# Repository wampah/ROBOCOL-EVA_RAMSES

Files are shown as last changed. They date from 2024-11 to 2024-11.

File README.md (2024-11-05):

# Mecanismo de extracción de muestras y laboratorio de evaluación de presencia de vida para un rover de exploración a distancia

Este repositorio contiene los archivos CAD y el código de Arduino del laboratorio de detección de vida alienígena, E.V.A. (Evaluador de Vida Alienígena), y del sistema de extracción de muestras, RAMSES (Recolector y Analizador de Muestras SuperficialES), desarrollados para el rover de la competencia University Rover Challenge (URC) 2022.

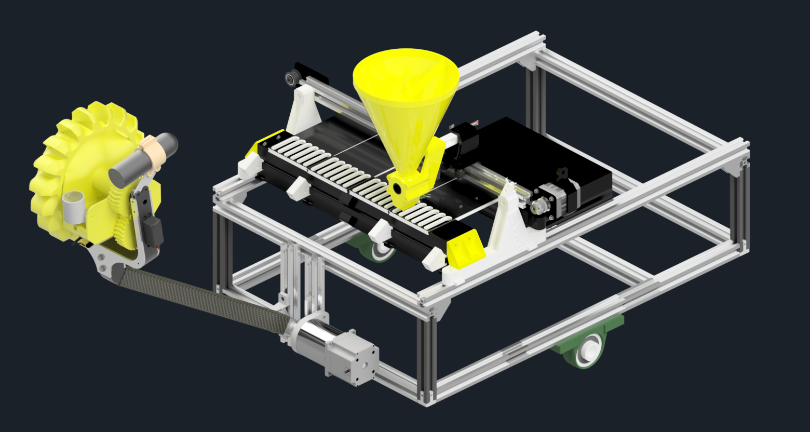
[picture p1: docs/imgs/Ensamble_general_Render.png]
Render EVA y RAMSES


## Descripción del Proyecto

### 1. **E.V.A. - Evaluador de Vida Alienígena**
E.V.A. es un sistema automatizado de análisis que permite la evaluación de vida alienígena en hasta 4 muestras simultáneas mediante 6 pruebas químicas distintas, ofreciendo datos sobre la presencia o ausencia de vida. Las muestras se distribuyen en 24 compartimentos mediante un actuador lineal de correa, y se dosifican utilizando un dispensador rotativo controlado por un servomotor de rotación continua y una válvula flexible en TPU. Una celda de carga mide el peso dosificado, y una cámara observa las reacciones químicas en cada compartimento. 

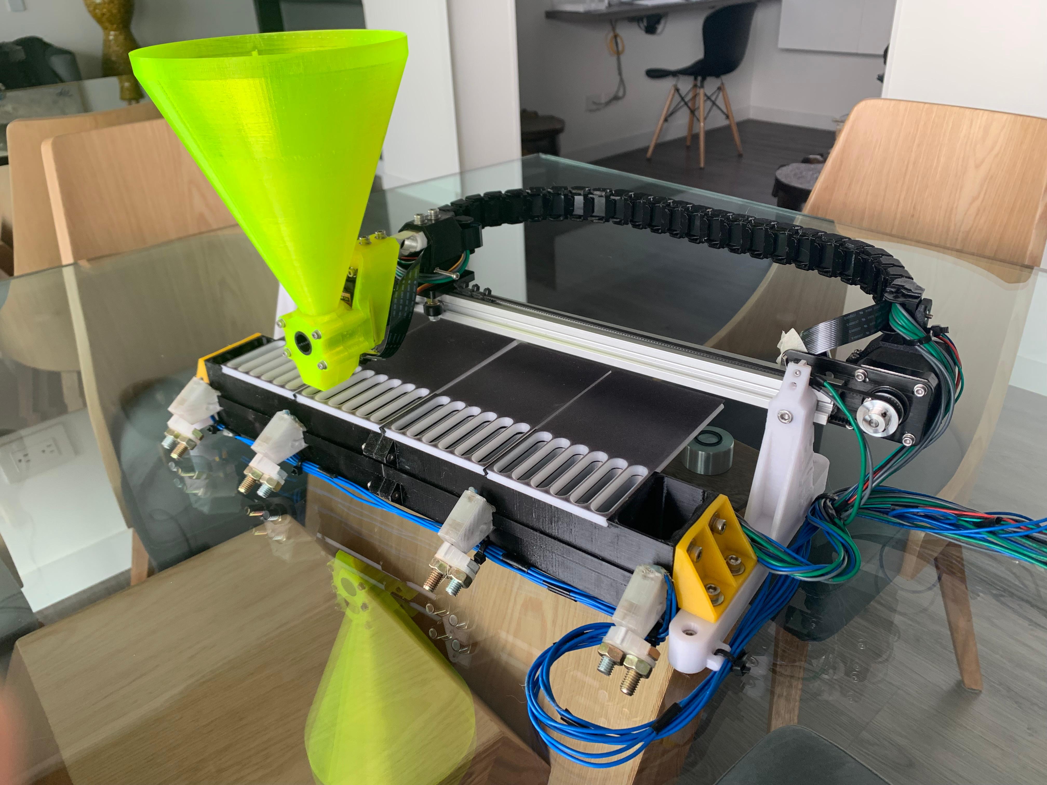
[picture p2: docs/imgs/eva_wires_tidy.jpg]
EVA


EVA gif

- **Pruebas químicas**: Detecta biomoléculas inorgánicas y orgánicas, como sales minerales y proteínas, usando reactivos especializados. 
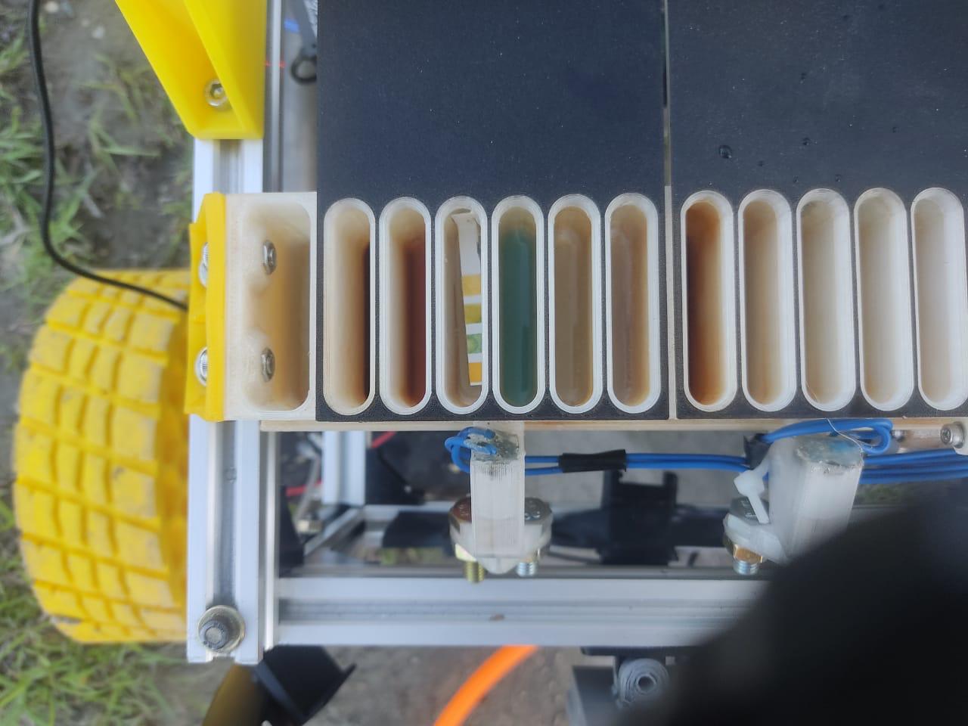
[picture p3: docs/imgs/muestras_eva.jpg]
EVA reactivos
  
- **Componentes principales**: Actuador lineal, servomotor, celda de carga, cámara, motores vibradores.
- **Fabricación**: Varias piezas fueron impresas en 3D, incluyendo compartimentos, tapas, soportes y el dispensador.

### 2. **RAMSES - Sistema de Extracción de Muestras**
RAMSES es el sistema encargado de recolectar, tamizar y medir la temperatura y humedad de las muestras antes de transferirlas a E.V.A. para su análisis. El sistema utiliza componentes impresos en 3D y un brazo controlado por un motor NEMA23 con reducción de 1:15, que permite el posicionamiento preciso del cabezal de excavación.

- **Funciones**: Recolección de muestras, tamizado, medición de temperatura y humedad.
- **Fabricación**: La mayoría de las piezas están fabricadas con impresión 3D.

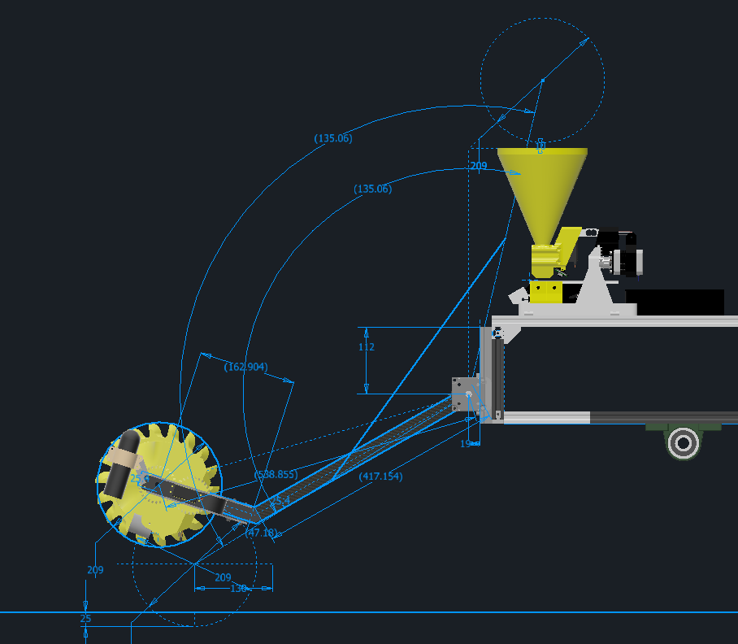
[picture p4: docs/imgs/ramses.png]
RAMSES


RAMSES gif

### 3. **Caja Electrónica**
La caja de electrónica aloja los componentes electrónicos del subsistema de sensórica y extracción, protegiéndolos de condiciones ambientales adversas. 

---

## Contenido del Repositorio

El repositorio se estructura en las siguientes carpetas y archivos:

- **Caja Electronica**: Archivos CAD de la caja de electrónica.
- **code**: Archivos de código de Arduino que controlan los subsistemas.
- **EVA**: Archivos CAD del sistema E.V.A.
- **Extras**: Archivos CAD complementarios.
- **Ready to print files**: Archivos CAD listos para impresión 3D de diversas piezas.
- **Sistema de extracción**: Archivos CAD del sistema RAMSES.
- **Ensamble general.iam**: Ensamble general del rover, integrando E.V.A., RAMSES y otros subsistemas.

## Instrucciones de Uso

1. **Montaje**: Ensamble los sistemas siguiendo los modelos CAD disponibles.
2. **Programación**: Cargue el código en los controladores Arduino. El sistema está configurado para comunicarse con una Raspberry Pi 4, conectada a través de serial para el control de actuadores y lectura de sensores.
3. **Operación**: Los reactivos se deben pre-cargar en los compartimentos de E.V.A. antes de la competencia. El sistema RAMSES extraerá muestras y las transferirá a E.V.A. para su análisis.

## Créditos y Equipo

El diseño, prototipado, y manufactura de estos sistemas fueron realizados por el equipo de Robocol de la Universidad de los Andes, en colaboración con miembros de diversas disciplinas. Estos sistemas formaron parte del rover de Robocol, que compitió en la URC 2022, y están diseñados para proporcionar datos relevantes para la detección de vida en condiciones simuladas de Marte.

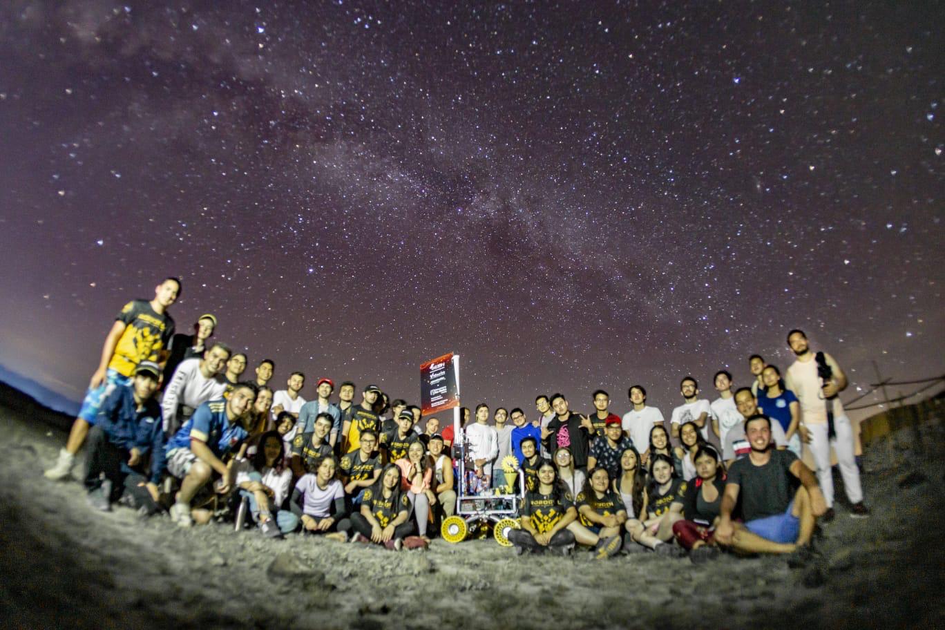
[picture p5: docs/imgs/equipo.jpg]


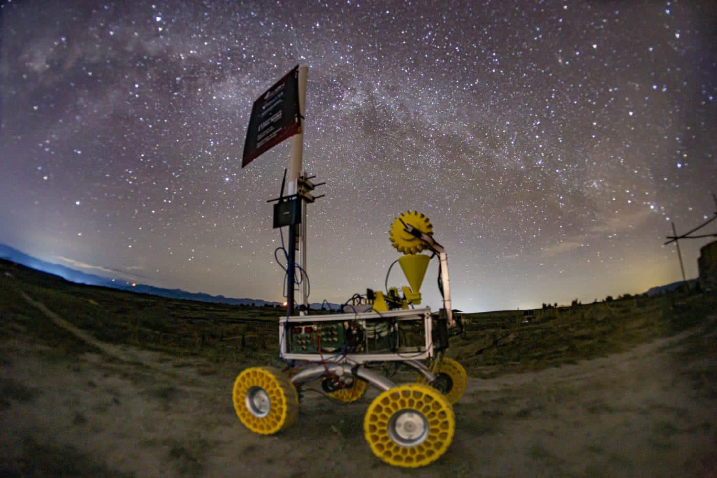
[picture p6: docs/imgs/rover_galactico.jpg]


### Contacto
Para consultas sobre este proyecto, puedes contactar a [Robocol](https://www.instagram.com/robocol/).

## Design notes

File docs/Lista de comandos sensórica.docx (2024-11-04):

Lista de comandos

¡¡¡¡Nota para sensórica -> TODOS LAS FUNCIONES DE MOVIMIENTO O QUE ESPERAN UNA ENTRADA DEBEN TENER TIMEOUT!!!!

ENVIAR UN MENSAJE DE READY O DE FINALIZACIÓN POR SERIAL

Mover el EVA (MOVE)

- M (# de compartimiento)
- Descripción:
  - Mueve el dispensador del EVA a la caja deseada.
- Notas:
  - El número de caja es un número de 2 dígitos. Rango [00,24].
- Ejemplos:
  - “M05“
  - “M24“

Abrir/cerrar cajas (BOX)

- B (# caja) (estado)
- Descripción:
  - Abre o cierra la puerta de la caja deseada.
- Notas:
  - El número de caja es un número de 1 dígito. Rango [1,4]
  - El estado es un dígito. Booleano. Rango [0,1]
- Ejemplos:
  - “B10“
  - “B11“
  - “B21“

Vibrar (SHAKE)

- S (tiempo en segundos)
- Descripción:
  - Agita las cajas del EVA por un tiempo determinado.
- Notas:
  - El tiempo es un número de 2 dígitos. Rango [00,99]
- Ejemplos:
  - “S05”
  - “S10”

Homear (HOME)

- H (sistema)
- Descripción:
  - Hace el home del sistema deseado (EVA o sistema de extracción)
- Notas:
  - El sistema es un carácter que indica el sistema. E para el EVA, X para el sistema de extracción. {“E”,”X”}
- Ejemplos:
  - “HE”
  - “HX”

Limpiar embudo (CLEAN)

- C (Velocidad)
- Descripción:
  - Determina la velocidad del motor de limpieza del embudo. En velocidad 0 se apaga.
- Notas:
  - La velocidad es un número de 1 carácter. Rango [0,5]
- Ejemplos:
  - “C0”
  - “C4”

Dispensar (DISPENSE)

- D (cantidad de muestra en gramos)
- Descripción:
  - Dispensa la cantidad de muestra deseada en gramos
- Notas:
  - La cantidad es un número de 2 dígitos. Rango [00,99]
- Ejemplos:
  - “D01”
  - “D05”

Encender/apagar sistemas (ENABLE)

- E (sistema) (estado)
- Descripción:
  - Habilita o deshabilita la potencia a los motores de paso del sistema deseado (EVA o sistema de extracción)
- Notas:
  - El sistema es un carácter que indica el sistema. E para el EVA, X para el sistema de extracción. {“E”,”X”}
  - El estado es un dígito. Booleano. Rango [0,1]
- Ejemplos:
  - “EE1”
  - “EX0”

Mover brazo (ARM)

- A (posición)
- Descripción:
  - Mueve el brazo a la posición superior o inferior
- Notas:
  - La posición es indicada por un carácter. U para la posición de arriba, D para la posición de extracción. {“U”,”D”}
- Ejemplos:
  - “AU“
  - “AD“

Extraer muestra (EXTRACT)

- X (velocidad) (tiempo)
- Descripción:
  - Gira la rueda de extracción a una velocidad determinada, por un tiempo determinado. El tamiz se prende mientras se extrae y se queda prendido un tiempo después para limpiarse.
- Notas:
  - La velocidad es un número de 1 carácter. Rango [0,5]
  - El tiempo es un número de 2 caracteres. Rango [00,99]
- Ejemplos:
  - “X105“
  - “X510“

Dejar muestra en el EVA (GATHER)

- G
- Descripción:
  - Dispensa la muestra recolectada por el sistema de extracción al EVA.
- Notas:
  - El sistema de extracción debe estar en la posición de arriba.
- Ejemplos:
  - “G“

COMANDOS DE CONTROL MANUAL:

Mover el EVA manualmente (MANUAL MOVE)

- -M (dirección) (distancia en mm)
- Descripción:
  - Mueve el dispensador del EVA manualmente.
- Notas:
  - La dirección es un dígito. Booleano. 0 indica mover en una dirección, 1 la otra dirección. Rango [0,1]
  - La distancia es un número de tres dígitos. Rango [000,999]
- Ejemplos:
  - “-M1100“
  - “-M0050“

Dispensar manualmente (MANUAL DISPENSE)

- -D (velocidad) (tiempo en segundos)
- Descripción:
  - Dispensa muestra manualmente
- Notas:
  - La velocidad es un número de 1 carácter. Rango [0,5]
  - El tiempo es un número de 1 carácter. Rango [0,9]
- Ejemplos:
  - “-D55”
  - “-D14”

Mover brazo manualmente (MANUAL ARM)

- -A (dirección) (distancia en grados)
- Descripción:
  - Mueve el brazo manualmente
- Notas:
  - La dirección es un dígito. Booleano. 0 indica mover en una dirección, 1 la otra dirección. Rango [0,1]
  - La distancia es un número de tres dígitos. Rango [000,999]
- Ejemplos:
  - “-A1100“
  - “-A0050“

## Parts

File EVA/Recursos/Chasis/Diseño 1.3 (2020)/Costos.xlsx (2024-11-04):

Costos Tracción
Componente | Referencia | Material | Costo/Unidad | Cantidad | Total
Rótula | PHS10 | Acero/Aluminio | 15126 | 6 | $90756.00
Chumacera | UCF 204-12 SS | Acero/Plástico | 40336 | 1 | $40336.00
Anillos Seeger | A 19 | Acero | 168 | 10 | $1680.00
IVA |  |  |  |  | $25226.68
 |  |  |  | Total Reprefer | $157998.68
 |  |  |  | En el recibo | $158000.00
Barra roscada | M10x1,5 de 1 m de largo | Acero | 9075.6 | 2 | $18151.20
Tornillos Bristol | M5 de 70 mm de largo | Acero | 420.17 | 20 | $8403.40
IVA |  |  |  |  | $5045.37
 |  |  |  | Total 7777777 | $31599.97
 |  |  |  | En el recibo | $31600.00
Potenciómetro | 20 K ohm de 10 vueltas | Plástico/Cobre/Acero | 13000 | 1 | $10530.00
IVA |  |  |  |  | $2470.00
 |  |  |  | Total Electrónicas Netronic | $13000.00
 |  |  |  | En el recibo | $13000.00
 | GRAN TOTAL | $202600.00

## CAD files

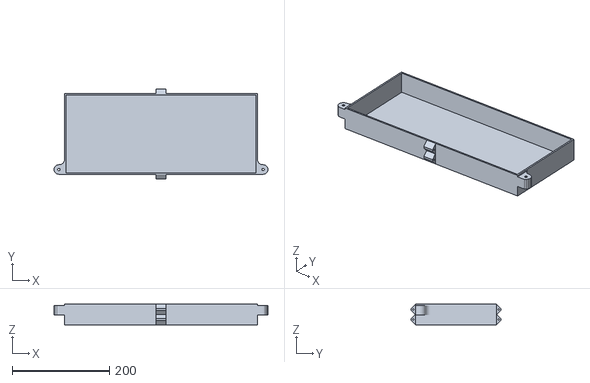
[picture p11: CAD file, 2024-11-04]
Caja Electronica/V2/Caja de electrónica.stl
440.0 x 184.6 x 43.0

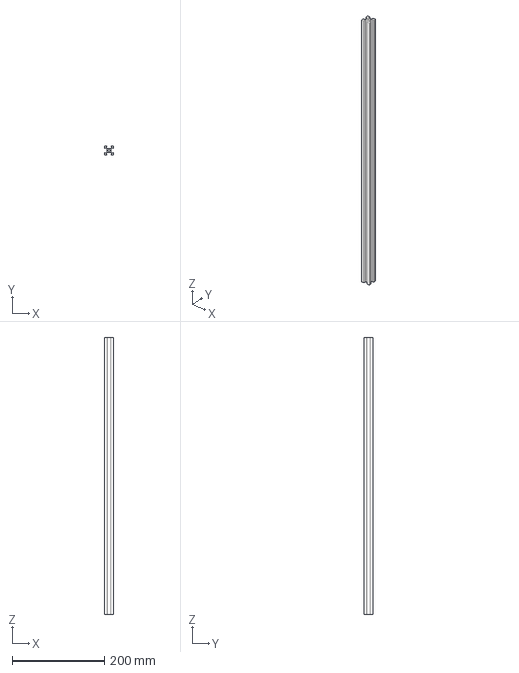
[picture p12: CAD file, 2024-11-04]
EVA/Recursos/Chasis/Diseño 1.3 (2020)/Step files/20x20mm L.stp
20.0 x 20.0 x 600.0 mm

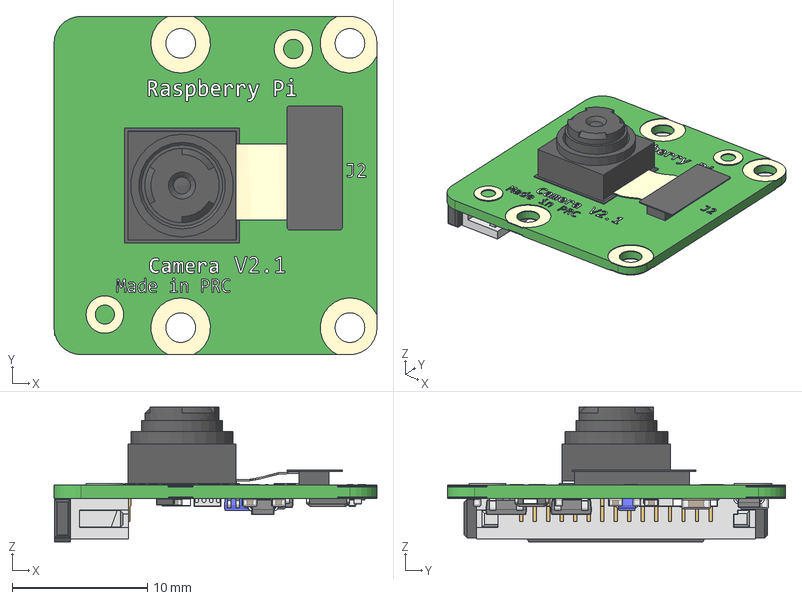
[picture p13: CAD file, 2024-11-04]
EVA/Recursos/Pi Camera/OTHER_FORMATS/RspCameraMia.stp
23.9 x 25.0 x 9.96 mm
PicameraPCB
OVA5647_Housing
OVA5647_Lens_FOV
ribbon_cam
CCD
CAPC-0805-T0.75-BN x 2
CAPC-0402-T0.55-BN x 10
RESC-0402 x 3
RESC-0603 x 2
RESC-1210
c-1-1734248-5-e-raspberry_display
SOT23-5 x 3
KX7 SMD Quartz Crystal Resonator 3.2x2.5mm
c6aaa
4pin_smd x 3

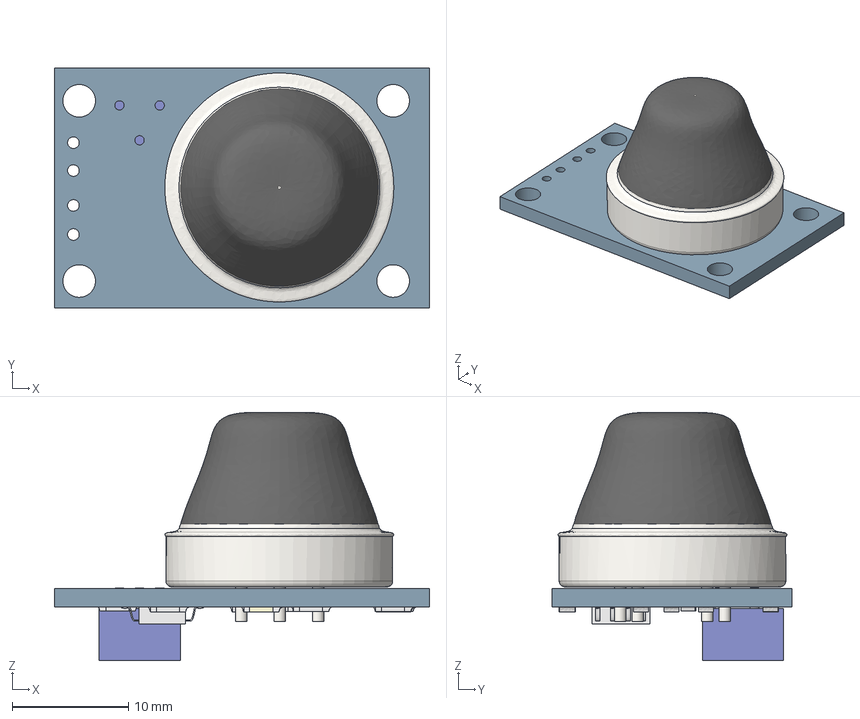
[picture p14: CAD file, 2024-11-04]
EVA/Recursos/Sensores/MQ2/MQ-2.step
32.2 x 20.6 x 21.4 mm
PCB
sensor
10k ohm SMT x 7
leads

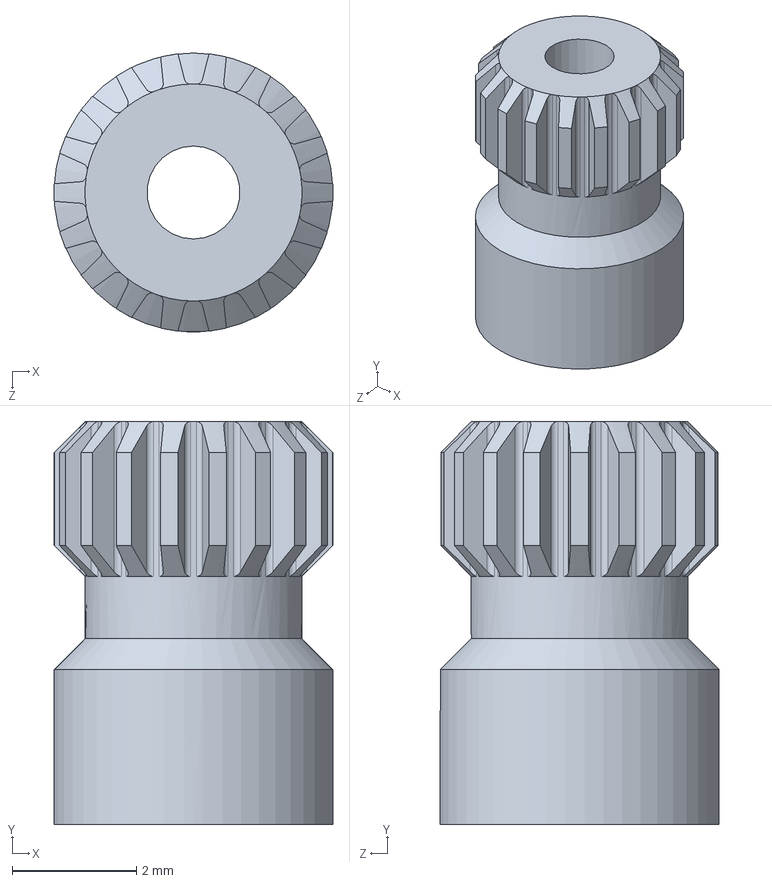
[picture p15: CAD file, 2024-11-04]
EVA/Recursos/Servo MG90S/Part4.SLDPRT
4.50 x 6.50 x 4.50 mm

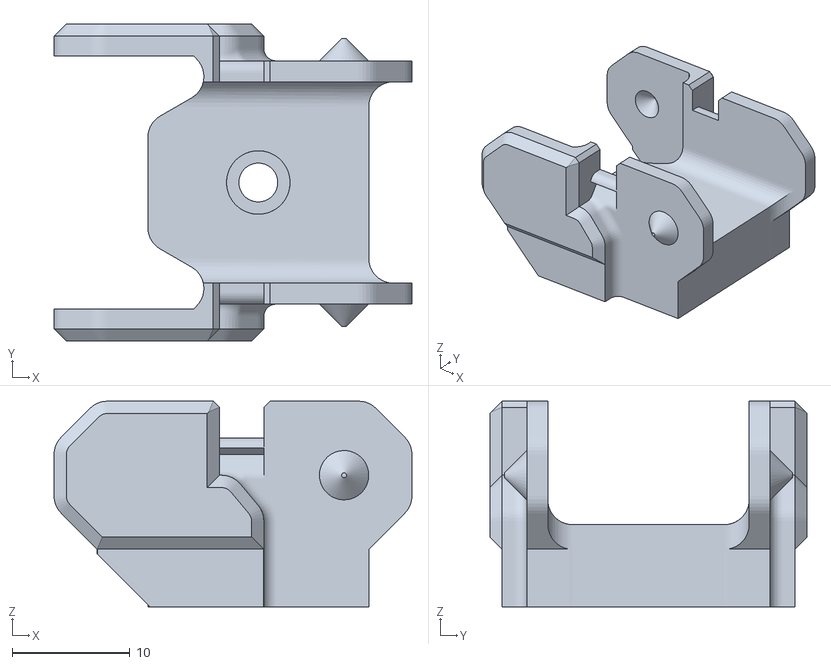
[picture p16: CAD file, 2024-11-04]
EVA/V3 (Actual)/Acople a chasis/Chainlink modificado.stl
30.5 x 27.0 x 17.5

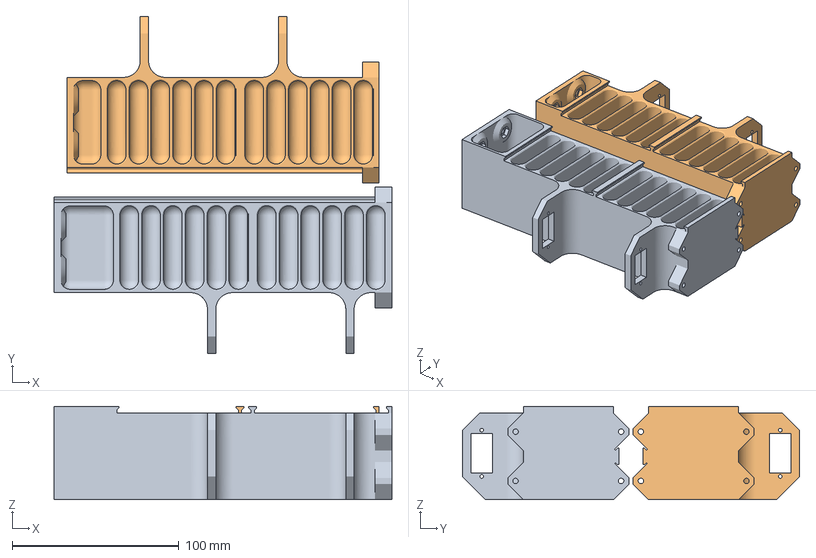
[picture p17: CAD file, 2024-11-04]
EVA/V3 (Actual)/cajas_V2.3mf
202.5 x 202.2 x 56.0 mm
cajas_V2.stl x 2

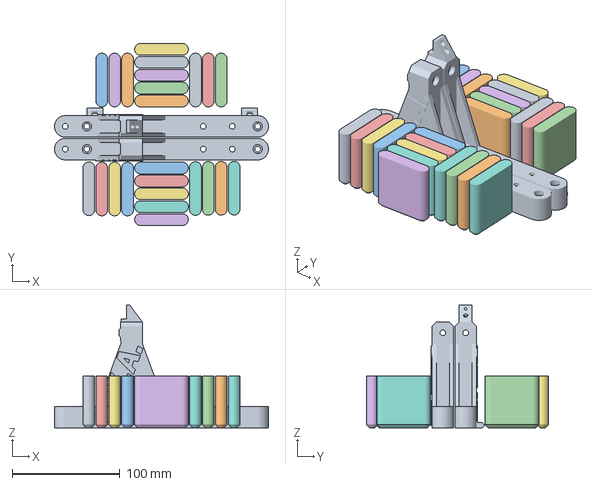
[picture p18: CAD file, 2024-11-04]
Ready to print files/Part2.3mf
198.5 x 168.8 x 114.0 mm
Merged
Part2.stl

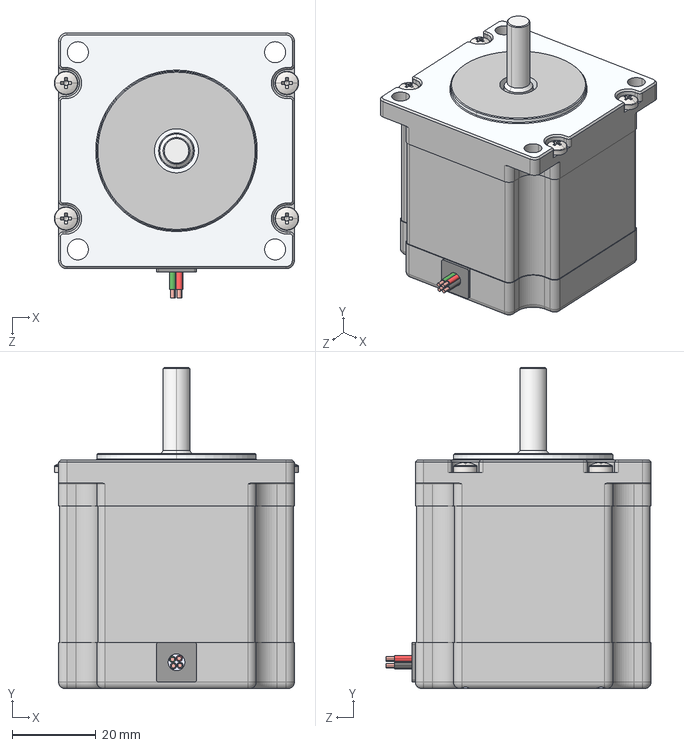
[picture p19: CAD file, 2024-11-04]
Sistema de extracción/V2 (Actual)/Brazo/NEMA 23 - 56mm.STEP
58.2 x 76.5 x 63.2 mm
NEMA 23 - 56mm
pan head cross recess screw_iso_ISO 7045 - M3 x 10 - Z - 10N x 4

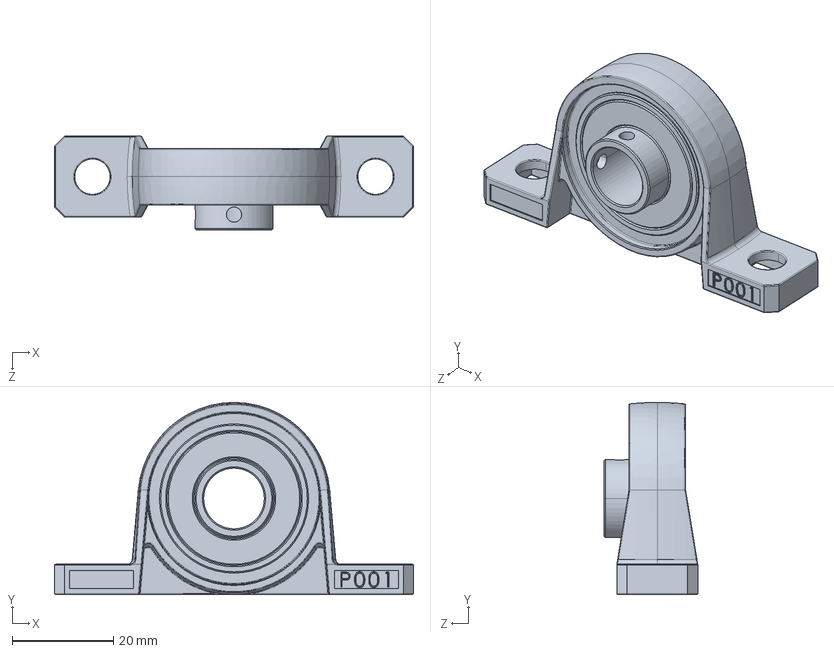
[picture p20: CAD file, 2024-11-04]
Sistema de extracción/V2 (Actual)/Recursos/Chumacera KP001/KP001_12.STEP
71.0 x 38.0 x 18.5 mm

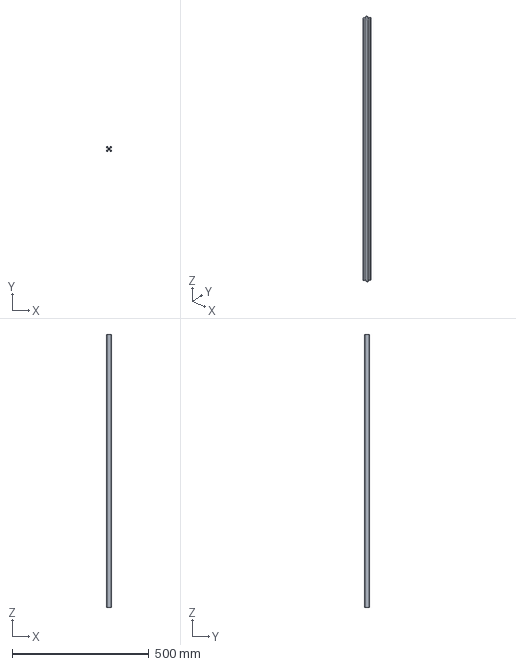
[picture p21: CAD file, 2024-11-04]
EVA/Recursos/Chasis/Diseño 1.3 (2020)/Step files/20x20x1000mm.stp
20.0 x 20.0 x 1000.0 mm

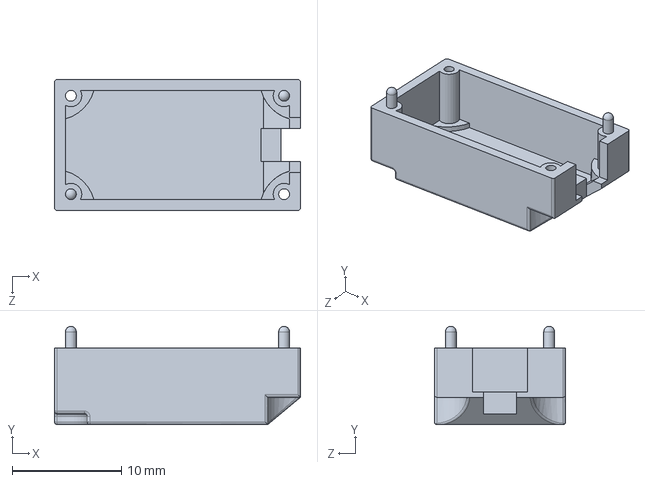
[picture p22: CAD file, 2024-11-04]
EVA/Recursos/Servo MG90S/Part1.SLDPRT
22.5 x 9.00 x 12.0 mm

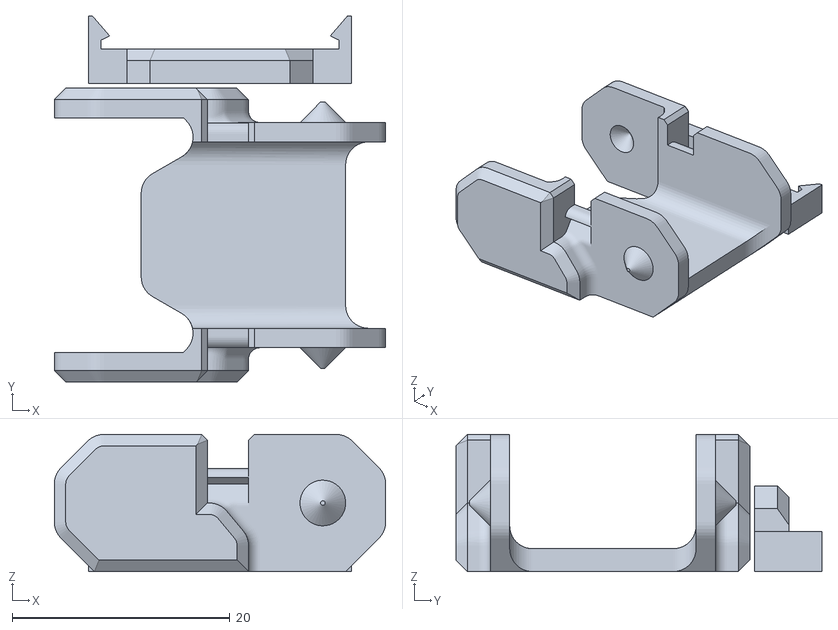
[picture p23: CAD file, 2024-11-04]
EVA/V3 (Actual)/Acople a chasis/Clip y Chainlink.stl
30.5 x 33.6 x 12.6

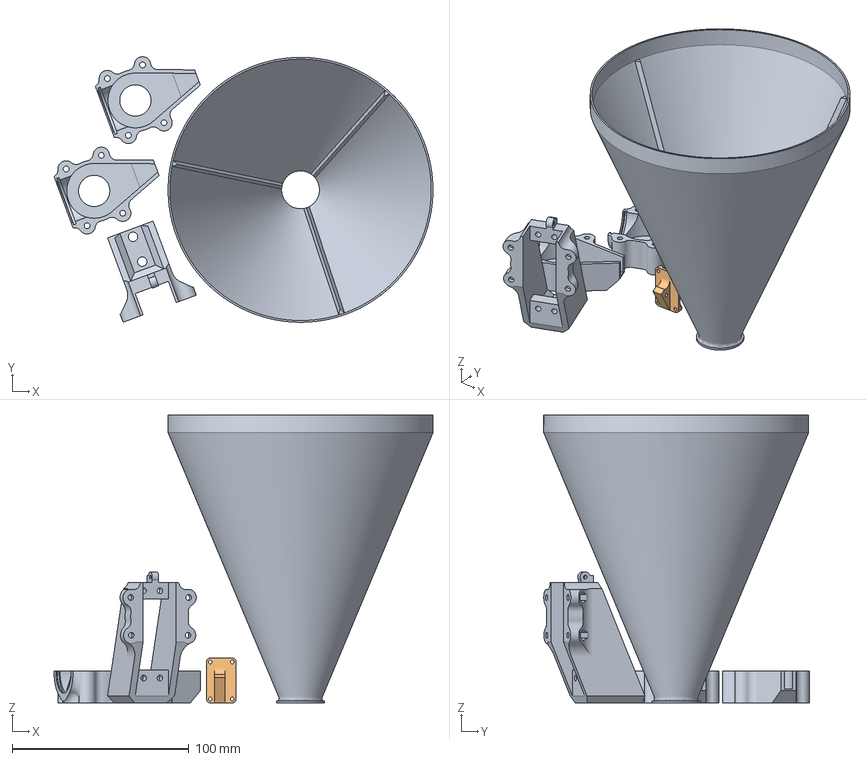
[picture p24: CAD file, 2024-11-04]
Ready to print files/Merged.3mf
214.6 x 150.4 x 163.0 mm
Merged
Case.stl

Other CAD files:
Sistema de extracción/V2 (Actual)/Brazo/Brazo.stp
EVA/Recursos/Chasis/Diseño 1.3 (2020)/Step files/20x20mm E.stp
EVA/Recursos/Servo MG90S/gear1.SLDPRT
Ready to print files/Contenedor anti-fuga (para imprimir en modo espiral).3mf
Caja Electronica/V1/Conectores1.ipt
Caja Electronica/V1/Conectores2.ipt
Caja Electronica/V1/Ensamble Cajas Electrónica.iam
Caja Electronica/V1/Ensamble.iam
Caja Electronica/V1/Espaciador.ipt
Caja Electronica/V1/Junta.ipt
Caja Electronica/V1/Junta.stl
Caja Electronica/V1/Main.stl
Caja Electronica/V1/OldVersions/Conectores1.0004.ipt
Caja Electronica/V1/OldVersions/Conectores2.0003.ipt
Caja Electronica/V1/OldVersions/Ensamble Cajas Electrónica.0005.iam
Caja Electronica/V1/OldVersions/Ensamble.0003.iam
Caja Electronica/V1/OldVersions/Junta.0003.ipt
Caja Electronica/V1/main_design.dxf
Caja Electronica/V1/one_connectors.dxf
Caja Electronica/V1/two_connectors.dxf
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

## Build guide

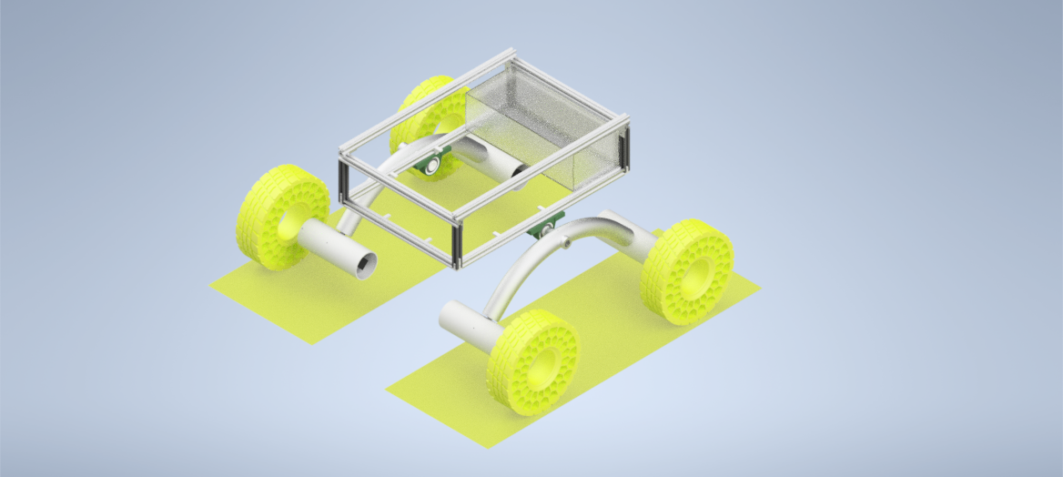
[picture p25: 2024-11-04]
EVA/Recursos/Chasis/Diseño 1.3 (2020)/Ensamblaje Rover.png

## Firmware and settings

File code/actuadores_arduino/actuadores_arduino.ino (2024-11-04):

//Librerias
#include <AccelStepper.h>
#include "HX711.h"
#include <Wire.h>
#include <Adafruit_PWMServoDriver.h>

//Parámetros STEPPER EVA
#define INTERFACE_EVA 1
#define MOTOR_STEPS_EVA 200
#define SPEED_EVA 600
#define ACCEL_EVA 2000
#define MICROSTEPS_EVA 4


//Parámetros STEPPER RAMSES
#define INTERFACE_RAMSES 1
#define MOTOR_STEPS_RAMSES 200
#define SPEED_RAMSES 100
#define ACCEL_RAMSES 20
#define MICROSTEPS_RAMSES 1

//Pines
#define EN_EVA 5
#define DIR_EVA 7
#define STEP_EVA 6

#define EN_RAMSES 8
#define DIR_RAMSES 10
#define STEP_RAMSES 9

#define PIN_FDC_B2 A3
#define PIN_FDC_B1 A2
#define PIN_FDC_EVA A1

#define PIN_VIB 12
#define PIN_TAMIZ 11

#define PIN_CELDA_DT A0
#define PIN_CELDA_SCK 13

#define PIN_LIMP_A 4
#define PIN_LIMP_B 2
#define PIN_LIMP_CTRL 3

//Canales PCA
#define servo_caja1 3
#define servo_caja2 1
#define servo_caja3 2
#define servo_caja4 0
#define servo_disp 4
#define servo_niv 5
#define servo_ex 6

//Constantes globales
const double factor_EVA = (200.0 / (59.54)) - 0.05; //Factor actuador lineal del EVA. Medidio y ajustado experimentalmente. Unidades [pasos/mm]

const double factor_RAMSES = 15.3 * 200.0 * (1.0 / 360.0); //Factor motor RAMSES. Calculado con la reducción de la caja. Unidaddes [pasos/grados]

const double distancias_cajas_mm[] =
{
  0,
  15.08333, 28.16667, 41.25000, 54.33333, 67.41667, 80.50000,
  97.58333, 110.66667, 123.75000, 136.83333, 149.91667, 163.00000,
  182.08333, 195.16667, 208.25000, 221.33333, 234.41667, 247.50000,
  264.58333, 277.66667, 290.75000, 303.83333, 316.91667, 330.00000
}; //Datos de distancias entre compartimientos. Obtenidos del diseño CAD. Unidades [mm]

const unsigned int pos0 = 172; // ancho de pulso para pocicion 0° (PCA)
const unsigned int pos180 = 565; // ancho de pulso para la pocicion 180° (PCA)
const unsigned int degs_reposo = 95; //Grados de reposo para servos de rotación continua

//Variables globales
String inputString = "";
char comando = "";
double peso_inicial = 0;
unsigned long tiempo;
boolean estado_EVA = false;
boolean estado_RAMSES = false;
String error_msg = "ERROR: ";

//Declaración STEPPER EVA
AccelStepper stepper_EVA(INTERFACE_EVA, STEP_EVA, DIR_EVA);

//Declaración STEPPER RAMSES
AccelStepper stepper_RAMSES(INTERFACE_RAMSES, STEP_RAMSES, DIR_RAMSES);

//Declaración PCA9685
Adafruit_PWMServoDriver servos = Adafruit_PWMServoDriver(0x40);

//Declaración de celda de carga
HX711 celda;

//Inicialización
void setup() {
  //Inicialización serial
  Serial.begin(57600);

  Serial.println("Initializing...");

  //Inicialización I2C
  Wire.begin();

  //Inicialización PCA9685 y señales iniciales. Frecuencia es 60Hz para servos. Servo dispensador esta quieto en 90/255.
  servos.begin();
  servos.setPWMFreq(60);
  servos.setPWM(servo_caja1, 0, pos0);
  servos.setPWM(servo_caja2, 0, pos0);
  servos.setPWM(servo_caja3, 0, pos0);
  servos.setPWM(servo_caja4, 0, pos0);
  servos.setPWM(servo_disp, 0, 1);
  servos.setPWM(servo_niv, 0, pos0);
  servos.setPWM(servo_ex, 0, pos0);

  //Inicialización STEPPERs
  stepper_EVA.setMaxSpeed(SPEED_EVA);
  stepper_EVA.setAcceleration(ACCEL_EVA);
  stepper_EVA.setEnablePin(EN_EVA);
  stepper_EVA.setPinsInverted(false, false, false);
  stepper_EVA.disableOutputs();


  stepper_RAMSES.setMaxSpeed(SPEED_RAMSES);
  stepper_RAMSES.setAcceleration(ACCEL_RAMSES);
  stepper_RAMSES.setEnablePin(EN_RAMSES);
  stepper_RAMSES.setPinsInverted(false, false, false);

  stepper_RAMSES.disableOutputs();
  estado_EVA = false;
  estado_RAMSES = false;

  //Inicialización y señal inicial pin rele de motores de vibración
  pinMode(PIN_VIB, OUTPUT);
  digitalWrite(PIN_VIB, HIGH);

  //Inicialización y señal inicial pin rele de tamiz
  pinMode(PIN_TAMIZ, OUTPUT);
  digitalWrite(PIN_TAMIZ, HIGH);

  //Inicalización pines DT y CLK celda de carga
  celda.begin(PIN_CELDA_DT, PIN_CELDA_SCK);

  //Inicialización de interruptores fin de carrera.
  pinMode(PIN_FDC_EVA, INPUT_PULLUP);
  pinMode(PIN_FDC_B1, INPUT_PULLUP);
  pinMode(PIN_FDC_B2, INPUT_PULLUP);

  //Inicialización motor de limpieza y señal inicial
  pinMode(PIN_LIMP_A, OUTPUT);
  pinMode(PIN_LIMP_B, OUTPUT);
  pinMode(PIN_LIMP_CTRL, OUTPUT);

  digitalWrite(PIN_LIMP_A, LOW);
  digitalWrite(PIN_LIMP_B, LOW);
  analogWrite(PIN_LIMP_CTRL, 0);

  Serial.println("EVA & RAMSES ready!");
}

//No se corre nada en el loop
void loop() {
}

//Función para encender o apagar el stepper del EVA.
void io_EVA(boolean estado) {
  if (estado) {
    stepper_EVA.enableOutputs();
    estado_EVA = true;
  }
  else {
    stepper_EVA.disableOutputs();
    estado_EVA = false;
  }
}

//Función para encender o apagar el stepper del RAMSES.
void io_RAMSES(boolean estado) {
  if (estado) {
    stepper_RAMSES.enableOutputs();
    estado_RAMSES = true;
  }
  else {
    stepper_RAMSES.disableOutputs();
    estado_RAMSES = false;
  }
}

//Función para hacer el home del EVA
void homear_EVA() {
  if (estado_EVA) {
    tiempo = millis();
    stepper_EVA.move(20000 * MICROSTEPS_EVA);
    while (digitalRead(PIN_FDC_EVA) == HIGH) {
      stepper_EVA.run();
      if (millis() - tiempo > 15000) {
        Serial.println(error_msg + "Timeout");
        return;
      }
    }
    stepper_EVA.stop();
    stepper_EVA.setCurrentPosition(0);
    stepper_EVA.runToNewPosition(-40);
    stepper_EVA.setMaxSpeed(SPEED_EVA * 0.25);
    stepper_EVA.move(20000 * MICROSTEPS_EVA);
    while (digitalRead(PIN_FDC_EVA) == HIGH) {
      stepper_EVA.run();
    }
    stepper_EVA.stop();
    stepper_EVA.setMaxSpeed(SPEED_EVA);
    stepper_EVA.runToNewPosition(-10 * MICROSTEPS_EVA);
    stepper_EVA.setCurrentPosition(0);

    delay(1000);
  }
  else {
    Serial.println(error_msg + "EVA stepper is not turned ON");
  }
}

//Función para hacer el home del RAMSES
void homear_RAMSES() {
  if (estado_RAMSES) {
    tiempo = millis();
    stepper_RAMSES.move(20000 * MICROSTEPS_RAMSES);
    while (digitalRead(PIN_FDC_B1) == HIGH) {
      stepper_RAMSES.run();
      if (millis() - tiempo > 15000) {
        Serial.println(error_msg + "Timeout");
        return;
      }
    }
    stepper_RAMSES.stop();
    stepper_RAMSES.setCurrentPosition(0);
    stepper_RAMSES.runToNewPosition(-40);
    stepper_RAMSES.setMaxSpeed(SPEED_RAMSES * 0.25);
    stepper_RAMSES.move(20000 * MICROSTEPS_RAMSES);
    while (digitalRead(PIN_FDC_B1) == HIGH) {
      stepper_RAMSES.run();
    }
    stepper_RAMSES.stop();
    stepper_RAMSES.setMaxSpeed(SPEED_RAMSES);
    stepper_RAMSES.runToNewPosition(-10 * MICROSTEPS_RAMSES);
    stepper_RAMSES.setCurrentPosition(0);
    delay(1000);
  }
  else {
    Serial.println(error_msg + "RAMSES stepper is not turned ON");
  }
}

//Función que mueve el dispensador del EVA automáticamente entre cajas.
void actuador_auto_EVA(int obj) {
  if (estado_EVA) {
    stepper_EVA.moveTo((int)(-MICROSTEPS_EVA *  factor_EVA * distancias_cajas_mm[obj]));
    while (stepper_EVA.distanceToGo() != 0) {
      stepper_EVA.run();
    }
  }
  else {
    Serial.println(error_msg + "EVA stepper is not turned ON");
  }
}

//Función que mueve el dispensador del EVA manualmente
void actuador_manual_EVA(boolean dir, double distancia_mm) {
  if (estado_EVA) {
    if (dir) {
      stepper_EVA.move((int)(MICROSTEPS_EVA * (factor_EVA * distancia_mm)));
      while (stepper_EVA.distanceToGo() != 0) {
        stepper_EVA.run();
      }
    }
    else {
      stepper_EVA.move((int)(-MICROSTEPS_EVA * (factor_EVA * distancia_mm)));
      while (stepper_EVA.distanceToGo() != 0) {
        stepper_EVA.run();
      }
    }
  }
  else {
    Serial.println(error_msg + "EVA stepper is not turned ON");
  }
}

//Función que mueve manualmente el brazo del RAMSES
void actuador_manual_RAMSES(boolean dir, double distancia_grados) {
  if (dir) {
    stepper_RAMSES.moveTo((int)(MICROSTEPS_RAMSES * factor_RAMSES * distancia_grados));
    while (stepper_RAMSES.distanceToGo() != 0) {
      stepper_RAMSES.run();
    }
  }
  else {
    stepper_RAMSES.moveTo((int)(-MICROSTEPS_RAMSES * factor_RAMSES * distancia_grados));
    while (stepper_RAMSES.distanceToGo() != 0) {
      stepper_RAMSES.run();
    }
  }
}

//Función que mueve automáticamente el brazo del RAMSES
void actuador_autom_RAMSES(boolean pos) {
  if (pos) {
    stepper_RAMSES.moveTo(0);
  }
  else {
    stepper_RAMSES.moveTo(600);
  }
}

//Función para abrir o cerrar las compuertas del EVA
void caja_EVA(int caja, boolean estado) {
  if (estado == true) {
    if (caja == 1) {
      servos.setPWM(servo_caja1, 0, deg2pulse(180));
    }
    else if (caja == 2) {
      servos.setPWM(servo_caja2, 0, deg2pulse(180));
    }
    else if (caja == 3) {
      servos.setPWM(servo_caja3, 0, deg2pulse(180));
    }
    else if (caja == 4) {
      servos.setPWM(servo_caja4, 0, deg2pulse(180));
    }
    else {}
  }
  else if (estado == false) {
    if (caja == 1) {
      servos.setPWM(servo_caja1, 0, deg2pulse(0));
    }
    else if (caja == 2) {
      servos.setPWM(servo_caja2, 0, deg2pulse(0));
    }
    else if (caja == 3) {
      servos.setPWM(servo_caja3, 0, deg2pulse(0));
    }
    else if (caja == 4) {
      servos.setPWM(servo_caja4, 0, deg2pulse(0));
    }
    else {}
  }
  else {}
  delay(1000);
}

//Función para activar los motores de vibración del EVA
void mezclar_EVA(int t_segundos) {
  digitalWrite(PIN_VIB, LOW);
  delay(t_segundos * 1000);
  digitalWrite(PIN_VIB, HIGH);
  delay(1000);
}
void limpiar_EVA(int vel) {
  if (vel == 0) {
    digitalWrite(PIN_LIMP_A, LOW);
    digitalWrite(PIN_LIMP_B, LOW);
  }
  else {
    digitalWrite(PIN_LIMP_A, LOW);
    digitalWrite(PIN_LIMP_B, HIGH);
    analogWrite(PIN_LIMP_CTRL, (int)(255.0 * ( (double)vel / 5)));
  }
  delay(1000);
}

void dispensar_manual_EVA(int vel, int t_segundos) {
  servos.setPWM(servo_disp, 0, deg2pulse((int)(90.0 - (90.0 * ( (double)vel / 5)))));
  delay(t_segundos * 1000);
  servos.setPWM(servo_disp, 0, deg2pulse(degs_reposo));
  delay(1000);
}

//FALTAAAAAAAAAAAAAAAAAAAAAAAAAAAAAAAAAAAAAAAAAAAAAAA
void tara() {
  peso_inicial = 0;
}
double pesar() {
  if (celda.is_ready()) {
    long reading = celda.read();
    Serial.print("HX711 reading: ");
    Serial.println(reading);
  } else {
    Serial.println("HX711 not found.");
  }
}

void serialEvent() {
  while (Serial.available()) {

    //Recibir Datos de Raspberry
    String inputString = Serial.readStringUntil('\n');
    Serial.print("You sent me: ");
    Serial.println(inputString);
    char comando = inputString.charAt(0);

    if (comando == 'm' || comando == 'M') {
      int compartimiento_temp = String(inputString.charAt(1)).toInt() * 10 + String(inputString.charAt(2)).toInt();
      if (compartimiento_temp <= 24 && compartimiento_temp >= 0) {
        Serial.println("Moving to comparment " + String(compartimiento_temp) + "...");
        actuador_auto_EVA(compartimiento_temp);
        Serial.println("Move to " + String(compartimiento_temp)+" finished");
      }
      else {
        Serial.println(error_msg + "Invalid compartment");
      }
    }
    if (comando == 'h' || comando == 'H') {
      char sistema_temp = inputString.charAt(1);
      if (sistema_temp == 'E' || sistema_temp == 'e') {
        Serial.println("Homing EVA...");
        homear_EVA();
        Serial.println("Homing EVA finished");
      }
      else if (sistema_temp == 'X' || sistema_temp == 'x') {
        Serial.println("Homing RAMSES...");
        homear_RAMSES();
        Serial.println("Homing RAMSES finished");
      }
      else {
        Serial.println(error_msg + "Invalid home");
      }
    }
    if (comando == 'e' || comando == 'E') {
      char sistema_temp = inputString.charAt(1);
      boolean estado_temp = false;

      if (sistema_temp == 'E' || sistema_temp == 'e') {
        if (String(inputString.charAt(2)).toInt() == 1) {
          io_EVA(true);
          Serial.println("EVA turned ON");
        }
        else if (String(inputString.charAt(2)).toInt() == 0) {
          io_EVA(false);
          Serial.println("EVA turned OFF");
        }
        else {
          Serial.println(error_msg + "Invalid status");
        }
      }
      else if (sistema_temp == 'X' || sistema_temp == 'x') {
        if (String(inputString.charAt(2)).toInt() == 1) {
          io_RAMSES(true);
          Serial.println("RAMSES turned ON");
        }
        else if (String(inputString.charAt(2)).toInt() == 0) {
          io_RAMSES(false);
          Serial.println("RAMSES turned OFF");
        }
        else {
          Serial.println(error_msg + "Invalid status");
        }
      }
      else {
        Serial.println(error_msg + "Invalid system");
      }
    }
    if (comando == 'b' || comando == 'B') {
      int caja_temp = String(inputString.charAt(1)).toInt();
      if (caja_temp >= 1 && caja_temp <= 4) {
        if (String(inputString.charAt(2)).toInt() == 1) {
          Serial.println("Opening box " + String(caja_temp));
          caja_EVA(caja_temp, false);
          Serial.println("Box " + String(caja_temp) + " is open");
        }
        else if (String(inputString.charAt(2)).toInt() == 0) {
          Serial.println("Closing box " + String(caja_temp));
          caja_EVA(caja_temp, true);
          Serial.println("Box " + String(caja_temp) + " is closed");
        }
        else {
          Serial.println(error_msg + "Invalid box state");
        }
      }
      else {
        Serial.println(error_msg + "Invalid box");
      }
    }
    if (comando == 's' || comando == 'S') {
      int t_mezclado_temp = String(inputString.charAt(1)).toInt() * 10 + String(inputString.charAt(2)).toInt();
      if (t_mezclado_temp > 0 && t_mezclado_temp <= 30) {
        Serial.println("Shaking samples for " + String(t_mezclado_temp) + " seconds");
        mezclar_EVA(t_mezclado_temp);
        Serial.println("Shaking finished");
      }
      else {
        Serial.println(error_msg + "Invalid shaking time");
      }
    }
    if (comando == 'd' || comando == 'D') {
      int vel_temp = String(inputString.charAt(1)).toInt();
      int t_disp_temp = String(inputString.charAt(2)).toInt();
      if (vel_temp > 0 && vel_temp <= 5) {
        if (t_disp_temp > 0 && t_disp_temp <= 9) {
          Serial.println("Dispensing sample at speed " + String(vel_temp) + " for " + String(t_disp_temp) + " seconds");
          dispensar_manual_EVA(vel_temp, t_disp_temp);
          Serial.println("Sample dispensed");
        }
        else {
          Serial.println(error_msg + "Invalid dispensing time");
        }
      }
      else {
        Serial.println(error_msg + "Invalid dispensing speed");
      }

    }
    if (comando == 'c' || comando == 'C') {
      int vel_temp = String(inputString.charAt(1)).toInt();
      if (vel_temp >= 0 && vel_temp <= 5) {
        limpiar_EVA(vel_temp);
        Serial.println("Cleaning speed set to " + String(vel_temp));
      }
      else {
        Serial.println(error_msg + "Invalid cleaning speed");
      }
    }
    if (comando == '-') {
      char comando_temp = inputString.charAt(1);
      if (comando_temp == 'd' || comando_temp == 'D') {
        int vel_temp = String(inputString.charAt(2)).toInt();
        int t_disp_temp = String(inputString.charAt(3)).toInt();
        if (vel_temp > 0 && vel_temp <= 5) {
          if (t_disp_temp > 0 && t_disp_temp <= 9) {
            Serial.println("Dispensing sample at speed " + String(vel_temp) + " for " + String(t_disp_temp) + " seconds");
            dispensar_manual_EVA(vel_temp, t_disp_temp);
            Serial.println("Sample dispensed");
          }
          else {
            Serial.println(error_msg + "Invalid dispensing time");
          }
        }
        else {
          Serial.println(error_msg + "Invalid dispensing speed");
        }

      }
      else if (comando_temp == 'a' || comando_temp == 'A') {
        int dir_temp = String(inputString.charAt(2)).toInt();
        double grados_temp = 100.0 * ((double)String(inputString.charAt(3)).toInt()) + 10.0 * ((double)String(inputString.charAt(4)).toInt()) + ((double)String(inputString.charAt(5)).toInt()) + 0.1 * ((double)String(inputString.charAt(6)).toInt());
        if (dir_temp == 1) {
          actuador_manual_RAMSES(true,  grados_temp);
        }
        else if (dir_temp == 0) {
          actuador_manual_RAMSES(false,  grados_temp);
        }
        else {
          Serial.println(error_msg + "Invalid sign");
        }
      }
      else if (comando_temp == 'm' || comando_temp == 'M') {
        int dir_temp = String(inputString.charAt(2)).toInt();
        double milimetros_temp = 100.0 * ((double)String(inputString.charAt(3)).toInt()) + 10.0 * ((double)String(inputString.charAt(4)).toInt()) + ((double)String(inputString.charAt(5)).toInt()) + 0.1 * ((double)String(inputString.charAt(6)).toInt());
        if (dir_temp == 1) {
          actuador_manual_EVA(true, milimetros_temp);
        }
        else if (dir_temp == 0) {
          actuador_manual_EVA(false, milimetros_temp);
        }
        else {
          Serial.println(error_msg + "Invalid sign");
        }
      }
      else {
        Serial.println(error_msg + "Invalid manual move command");
      }
    }
    comando = "";
    inputString = "";
  }
}

int deg2pulse(int deg) {
  return map(deg, 0, 180, pos0, pos180);
}
